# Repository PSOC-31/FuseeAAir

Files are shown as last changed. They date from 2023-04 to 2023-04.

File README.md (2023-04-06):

# FuseeAAir
Sources matérielles et pédagogiques autour des fusées à air utilisées à Planète Sciences Occitanie
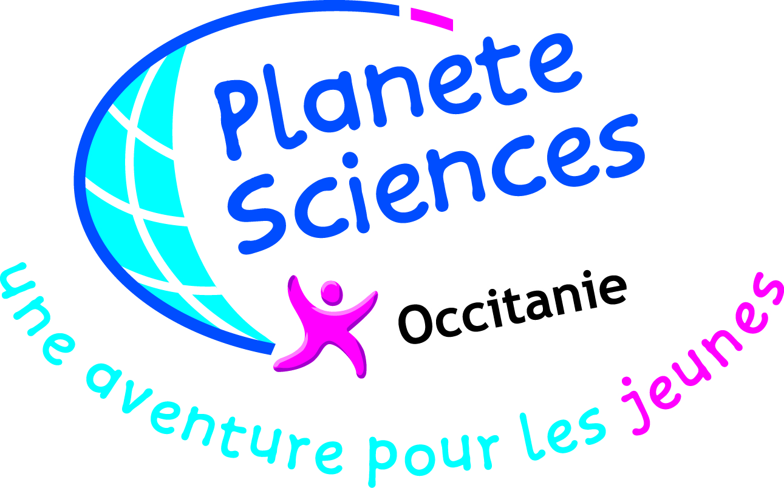
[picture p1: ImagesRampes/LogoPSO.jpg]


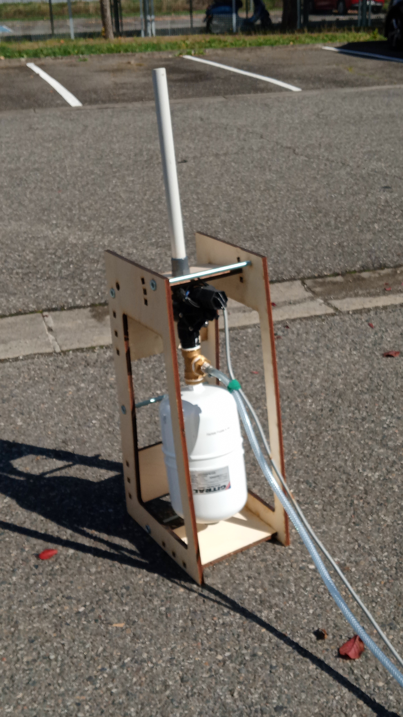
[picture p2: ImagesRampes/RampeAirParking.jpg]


## Notes de versions. 

Attention, les versions citées sont celles des versions matérielles, non pas celles du présent document, lui-même bien moins souvent mis à jour que le matériel.

-   V1 Base initiale dont le réservoir d'air est constitué d'un tube PVC pour conduite d'eau pression (genre piscine) diamètre 90 (à vérifier) , d'un raccord en T et divers raccords et bouchons. A été reproduit en quelques exemplaires, mais chaque fois avec des fuites sans possibilité de rattrapage parce que non-démontable.

-   V2 Version dont le réservoir est constitué d'un raccord femelle-femelle diamètre 100, d'un tampon de visite et de divers raccord. Présente l'avantage d'être démontable pour rattraper les mauvais collages, mais nous avons eu des explosions lors d'animations.

-   V3 Version dont le réservoir est constitué d'un vase d'expansion vendu garanti pour 10 bars.

    -   V 3.0 Version initiale. Le support bois découpé laser consomme 4 planches 300\*600 e10.
    -   V 3.1 Support bois à flancs ajourés sur 2 planches.
    -   V3.2 Divers ajustements sur le support. Quelques problèmes récurrents d'introduction en travers des raccords métal/plastique.
    -   V 3.3 Utilisation d'un T 1 pouce au lieu de 3/4 de pouce, ce qui permet de limiter les destructions de filetages plastique, en particulier au niveau de l'électro-vanne. Ajustement du support.
    -   V 3.4 Ajustement du support.
    -   V3.5 Version de travail du document de fabrication intermédiaire
    -   V3.6 Mise au propre des documents pour publication sur https://github.com/PSOC-31

## Inventaire des éléments

  ---------------------------------------------------------------------------- ----------------------------------------- --------------------- ----------------- ------ ------- -------
  Electro vanne                                                                1\" FF JTV 9V RBIRD                       IrriJardin            421020            1      49,99   54,42
  Vase d'expension Gitral HY5                                                  Partedis                                  Partedis              17119             1      54,42   54,42
  Tube renforcé 7\*13                                                          rlx 25m pvc tresse 7\*13                  CIR                   1025V130007       5      45,72   9,14
  Té laiton FFF 26X34 1pouce                                                                                             Partedis              29407             1      8,3     8,3
  Réduction laiton MF 6 pans JT plat 26-20                                                                               Partedis              68472             1      2,54    2,54
  Réduction laiton MF 6 pans JT plat 26-15                                                                               Partedis              68467             1      3,91    3,91
  Réduction laiton MF 6 pans JT plat 15-8                                                                                Partedis              68320             1      1,06    1,06
  Mamelon MM 6 pans plastique 1pouce                                                                                     IrriJardin            181755            1      5       5
  Tétine (à refaire)                                                           douille cann male co.gaz                  CIR                   1230717           1      5,55    5,55
  Collier                                                                      6 colliersgalva 9-16 sachet l8mm          Leroy Merlin Balma    h 80153727        2      3,25    1,08
  Pompe a pied 500                                                             Pompe a pied 500                          Decatlon escalquens   1829519           1      16      16
  Valve pour roue voiture                                                                                                Feu Vert                                1      0       0
  Raccord fileté PVC                                                           Raccord fil Pvc M32 F25 26\*34            IrriJardin            120639            1      3,4     3,4
  Tube IRO                                                                     Tube tulipe irl lm d25mm gris 2.5m        Leroy Merlin Balma    h3447640069375    0,35   1,35    0,19
  Tampon de visite d40                                                         bouchon D40                               Leroy Merlin Balma    h 3343340668804   2      0,65    1,3
  Manchon ff d40                                                               Manchon ff d40                            Leroy Merlin Balma    h 3343340465205   2      0,25    0,5
  Tube écoulement d40                                                                                                    Leroy Merlin Balma                      2      0,15    0,15
  Fil électrique double conducteur, double isolation, souple.                                                                                                    6              0
  Connecteur pile 9V                                                                                                                                             1              0
  Interrupteur à bascule marche-arrêt 12mm avec couvercle de protection 1021   AliExpress                                088 electric Store                      1      1,89    1,89
  Pile 9V                                                                                                                Opitec                                  1      20,99   2,1
  Planche CTP 10 mm 300\*600                                                   FabRiquet                                                                         2      10      20
  Découpe laser                                                                FabRiquet                                                                         0,33   40      13,2
  Tige filetée M10                                                                                                       Castorama                               0,25   1,9     0,48
  Ecrou façon rondelle M10                                                     Ecrou emb. Crantée din -çé » ZG M10 X25   Bricoman                                4      5       0,8
  Rondelle large 10                                                            Rondelles extralarge ZG D10X36X2 X25      Bricoman                                4      3,58    0,57
  Ecrou papillon                                                                                                                                                 4      1,09    1,09
                                                                                                                                                                                
  Total                                                                                                                                                                         207,1
  ---------------------------------------------------------------------------- ----------------------------------------- --------------------- ----------------- ------ ------- -------

## Montage de la chambre de pression.

La chambre de pression est le volume d'air immédiatement à l'arrière de l'électrovanne. C'est le vase d'expansion, les divers raccords et le tuyau de gonflage qui sont sous pression, dans l'attente du lancement.

La première étape consiste a assembler entre eux les éléments de la chambre de pression afin qu'il ne forme qu'un seul élément.

## Généralités sur l'étanchéité.

L'ensemble des parties sous pression devront supporter plusieurs bars. L'étanchéité du montage des raccords est donc primordial. D'une façon générale, l'utilisation de joints est largement recommandé, mais pour cela il est nécessaire qu'une surface d'appui existe, ce qui n'est pas le cas dans l'ensemble des objets choisi. Après avoir essayé diverses solutions, de la pâte spécialisée au fil imprégné, ma préférence personnelle reste au ruban PTFE (Téflon, antonomase). Je recommande sur un montage métal-métal de faire au moins une dizaine de tours, dans le sens du dévissage pour éviter le déroulement lors de l'introduction. Si lors des essais en pression dans un bac d'eau, on voit apparaître des fuites, on peu démonter le raccord et ajouter des tours supplémentaires. Sur un raccord plastique-métal ou plastique-plastique, il faut généralement moins de tours.

Attention au début du vissage, on part très vite en travers, surtout dans les montages métal-plastique, et on a tendance à flinguer la partie plastique. Je recommande, lors de la pose du ruban PTFE, d'épargner les premiers millimètres. Ça aide à une introduction correcte.

## Montage des raccords.

-   Monter sur la partie perpendiculaire du raccord en T femelle/femelle/femelle 1 pouce (26X34), la réduction mâle-femelle 26-15.
-   Sur cette même réduction, monter une tétine mâle XXX pour tuyau 7\*13.
-   Sur une branche du T, monter un mamelon double mâle-mâle 1 pouce (26X34) en plastique.
-   Sur ce mamelon, monter l'électrovanne, coté entrée (empennage de la flèche sur l'électrovanne).
-   De l'autre coté de ce mamelon, en face sur l'autre branche du T, visser une réduction femelle-femelle 26-20.
-   Dans ce dernier mamelon, visser le vase d'expansion 5 litres.

## Montage de la ligne de gonflage.

Voir le document commun pour les rampes fusée à eau et rampes fusée à air « Fabrication de la ligne de gonflage pour Bases de lancement Fusées à Air et Fusées à Eau. V1.1 »

## Montage de la commande de l'électrovanne.

Il y a plusieurs types d'électrovannes. Certaines sont nominalement alimentées en 24V. Je suppose que c'est pour se prémunir contre les possibles pertes en lignes dues à de très longs câblages dans un champ. Pour une utilisation à notre pression, avec de l'air et avec un câblage soigné, une tension nominale de 9V est suffisante. Cependant, je recommande l'utilisation de piles alcalines.



Le boîtier de commande est un assemblage de tubes d'écoulement d'eau de diamètre 40.

Poncez-collez deux manchons femelle/femelle sur une longueur de tube de 60 mm. Au extrémités des manchons, collez les tampons de visite en ayant préalablement dévissé les bouchons des tampons.

Percez et usinez les bouchons pour, d'un coté, placer l'interrupteur,

 de l'autre pour faire passer un câble électrique type double conducteur, double isolation, souple, de 6 mètres.

Taillez un bout de polystyrène extrudé ou de la mousse un peu dure, diamètre 30, épaisseur 20, pour caler la pile 9V.



Montez et câblez un interrupteur sur un bouchon de tampon. Vissez ce bouchon et câblez le connecteur de pile et le câble secteur. Bien sûr, vous n'avez pas oublié de faire passer ce câble dans le trou de l'autre bouchon!

Glissez d'abord la cale en polystyrène, puis la pile connectée. Placez un collier de serrage plastique (Rislan ou Colson, antonomase ) sur le câble, et serrez bien. Vissez le bouchon en faisant quelques tours en arrière avant de visser (pour éviter d'avoir un câble vrillé à l'intérieur).

Connectez l'électrovanne à l'autre extrémité en soudant et utilisant de la gaine gaine thermo-rétractable et thermo-collante.

Fixez le câble à l'électro-vanne avec un collier de serrage plastique (Rislan ou Colson, antonomase ).

## Configuration du vase d'expansion.

Le vase d'expansion est prévu pour permettre une dilatation de l'eau dans un circuit (cas de la partie chaude de l'eau sanitaire), sans mettre en contact l'eau avec l'air pour limiter l'oxydation des parties métalliques. Par construction, il existe une chambre à air intégrée dans le vase, gonflé à 2 bars. Pour notre utilisation, il est nécessaire de dégonfler entièrement cette chambre pour profiter de la vitesse maximum d'éjection de l'air. Donc, dans un premier temps, on va dévisser le protége-cul du vase, et appuyer avec un objet quelconque sur la valve pour dégonfler.

Photo à venir.

Ensuite, pressuriser avec la pompe à vélo le circuit principal (dans le vase, pour chasser le reste d'air de la chambre) et recommencer à appuyer sur la valve. Refaire 2 ou 3 fois cette opération pour vider complètement la chambre.

## Tests de l'ensemble.

Testez le montage en plongeant l'ensemble sous pression (2 bars mini) dans l'eau. N'oubliez pas de tester les deux extrémités du tuyau d'air.

Pour les raccords filetés, voir note «Généralités sur l'étanchéité» en début de notice.

Pour les raccords avec collier inox, un resserrage suffit la plupart du temps.

De plus, un test à pression élevé est recommandé (je dirais env 6 bars mais pas plus de 10, limite de la garantie du vase d'expansion) en prenant des précautions en cas d'éclatement, genre carton ou couverture autour. Attention, à forte pression, il arrive que l'électro-vanne ne se déclenche pas. La dépressurisation peux se faire à distance en déconnectant la pompe à vélo et agir mécaniquement sur la valve du tube. Pour une utilisation dans ces pressions, on peu envisager un déclenchement avec 2 plies 9v, donc 18v.

## Fabrication du support.

### Tube de lancement.

Coupez une longueur de 350 mm de tube IRO (isolant rigide ordinaire) ou IRL (isolant rigide lisse), et non pas ICTA (isolant cintrable transversalement annelé*), *vendu en rayon électricité, de diamètre 32. Collez-le sur un raccord fileté Pvc M32 F25 26\*34. Laisser sécher au moins 24h.

Cet ensemble tube/raccord sert au montage de l'ensemble actif de la rampe sur le support en bois et permet de rentrer une rampe, voire deux, dans une malle.

N'oubliez pas dans les achats les longueurs de tube IRO nécessaires en tant que mandrin pour la fabrication des fusées elles-mêmes. Leur nombre dépendra du nombre d'enfants par atelier.

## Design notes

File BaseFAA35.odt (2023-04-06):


Fabrication Bases de lancement Fusées à Air. V3.5

Photo à insérer

# Notes de versions.

Attention, les versions citées sont celles des versions matérielles, non pas celles du présent document, lui-même bien moins souvent mis à jour que le matériel.

- V1 Base initiale dont le réservoir d’air est constitué d’un tube PVC pour conduite d’eau pression (genre piscine) diamètre 90 (à vérifier) , d’un raccord en T et divers raccords et bouchons. A été reproduit en quelques exemplaires, mais chaque fois avec des fuites sans possibilité de rattrapage parce que non-démontable.
- V2 Version dont le réservoir est constitué d’un raccord femelle-femelle diamètre 100, d’un tampon de visite et de divers raccord. Présente l’avantage d’être démontable pour rattraper les mauvais collage, mais nous avons eu des explosions lors d’animations.
- V3 Version dont le réservoir est constitué d’un vase d’expansion vendu garanti pour 10 bars.
  - V 3.0 Version initiale. Le support bois découpé laser consomme 4 planches 300*600 e10.
  - V 3.1 Support bois à flancs ajourés sur 2 planches.
  - V3.2 Divers ajustements sur le support. Quelques problèmes récurrents d’introduction en travers des raccords métal/plastique.
  - V 3.3 Utilisation d’un T 1 pouce au lieu de 3/4 de pouce, ce qui permet de limiter les destructions de filetages plastique, en particulier au niveau de l’électro-vanne. Ajustement du support.
  - V 3.4 Ajustement du support.

# Inventaire des éléments

Tableau à venir

# Montage de la chambre de pression.

La chambre de pression est le volume d’air immédiatement à l’arrière de l’électrovanne. C’est le vase d’expansion, les divers raccords et le tuyau de gonflage qui sont sous pression, dans l’attente du lancement.

La première étape consiste a assembler entre eux les éléments de la chambre de pression afin qu’il ne forme qu’un seul élément.

## Généralités sur l’étanchéité.

L’ensemble des parties sous pression devront supporter plusieurs bars. L’étanchéité du montage des raccords est donc primordial. D’une façon générale, l’utilisation de joints est largement recommandé, mais pour cela il est nécessaire qu’une surface d’appui existe, ce qui n’est pas le cas dans l’ensemble des objets choisi. Après avoir essayé diverses solutions, de la pâte spécialisée au fil imprégné, ma préférence personnelle reste au ruban PTFE (Téflon, antonomase). Je recommande sur un montage métal-métal de faire au moins une dizaine de tours, dans le sens du dévissage pour éviter le déroulement lors de l’introduction. Si lors des essais en pression dans un bac d’eau, on voit apparaître des fuites, on peu démonter le raccord et ajouter des tours supplémentaires. Sur un raccord plastique-métal ou plastique-plastique, il faut généralement moins de tours.

Attention au début du vissage, on part très vite en travers, surtout dans les montages métal-plastique, et on a tendance à flinguer la partie plastique. Je recommande, lors de la pose du ruban PTFE, d’épargner les premiers millimètres. Ça aide à une introduction correcte.

# Montage de la ligne de gonflage.

Voir le document commun pour les rampes fusée à eau et rampes fusée à air « Fabrication de la ligne de gonflage pour Bases de lancement Fusées à Air et Fusées à Eau. V1.1 »

# Montage de la commande de l’électrovanne.

Nominalement, l’électrovanne est alimenté en 24V. Je suppose que c’est pour se prémunir contre les possibles pertes en lignes dues à de très longs câblages dans un champ. Pour une utilisation à notre pression, avec de l’air et avec un câblage soigné, une tension nominale de 9V est suffisante. Cependant, je recommande l’utilisation de piles alcalines.

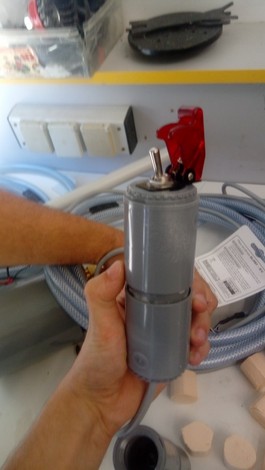
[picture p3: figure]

Le boîtier de commande est un assemblage de tubes d’écoulement d’eau de diamètre 40.

Poncez-collez deux manchons femelle/femelle sur une longueur de tube de 60 mm. Au extrémités des manchons, collez les tampons de visite en ayant préalablement dévissé les bouchons des tampons.

Percez et usinez les bouchons pour, d’un coté, placer l’interrupteur, de l’autre pour faire passer un câble électrique type double conducteur, double isolation, souple, de 6 mètres.

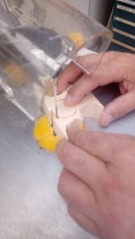
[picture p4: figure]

Taillez un bout de polystyrène extrudé diamètre 30, épaisseur 20, pour caler la pile 9V.

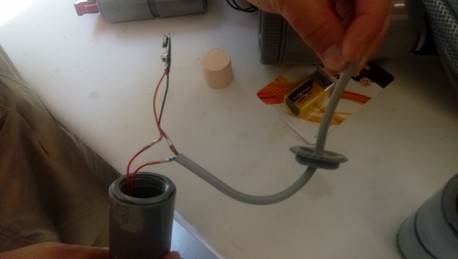
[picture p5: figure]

Montez et câblez un interrupteur sur un bouchon de tampon. Vissez ce bouchon et câblez le connecteur de pile et le câble secteur. Bien sûr, vous n’avez pas oublié de faire passer ce câble dans le trou de l’autre bouchon!

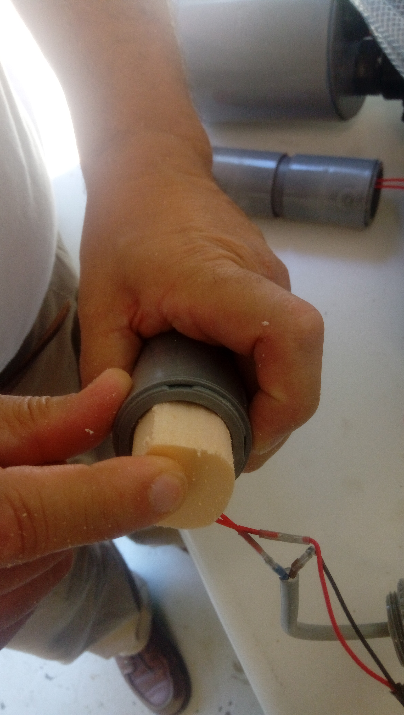
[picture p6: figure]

Glissez d’abord la cale en polystyrène, puis la pile connectée. Placez un collier de serrage plastique (Rislan ou Colson, antonomase ) sur le câble, et serrez bien. Vissez le bouchon en faisant quelques tours en arrière avant de visser (pour éviter d’avoir un câble vrillé à l’intérieur).

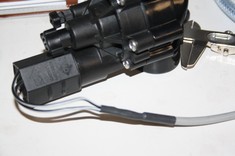
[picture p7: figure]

Connectez l’électrovanne à l’autre extrémité en soudant et utilisant de la gaine gaine thermo-rétractable et thermo-collante.

Fixez le câble à l’électro-vanne avec un collier de serrage plastique (Rislan ou Colson, antonomase ).

Photo à venir.

# Tests de l’ensemble.

Testez le montage en plongeant l’ensemble sous pression (2 bars mini) dans l’eau. N’oubliez pas de tester les deux extrémités du tuyau d’air.

Pour les raccords filetés, voir note «Généralités sur l’étanchéité» en début de notice.

Pour les raccords avec collier inox, un resserrage suffit la plupart du temps.

De plus, un test à pression élevé est recommandé (je dirais env 6 bars mais pas plus de 10, limite de la garantie du vase d’expansion) en prenant des précautions en cas d’éclatement, genre carton ou couverture autour. Attention, à forte pression, il arrive que l’électro-vanne ne se déclenche pas. La dépressurisation peux se faire à distance en déconnectant la pompe à vélo et agir mécaniquement sur la valve du tube. Pour une utilisation dans ces pressions, on peu envisager un déclenchement avec 2 plies 9v, donc 18v.

# Fabrication du support.

# Tube de lancement.

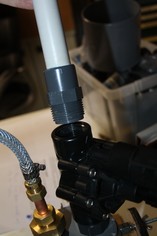
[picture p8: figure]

Coupez une longueur de 350 mm de tube IRO (isolant rigide ordinaire) ou IRL (isolant rigide lisse), et non pas ICTA (isolant cintrable transversalement annelé), vendu en rayon électricité, de diamètre 32. Collez-le sur un raccord fileté Pvc M32 F25 26*34. Laisser sécher au moins 24h.

Cet ensemble tube/raccord sert au montage de l’ensemble actif de la rampe sur le support en bois et permet de renter une rampe, voire deux, dans une malle.

N’oubliez pas dans les achats les longueurs de tube IRO nécessaires en tant que mandrin pour la fabrication des fusées elles-mêmes. Leur nombre dépendra du nombre d’enfants par atelier.

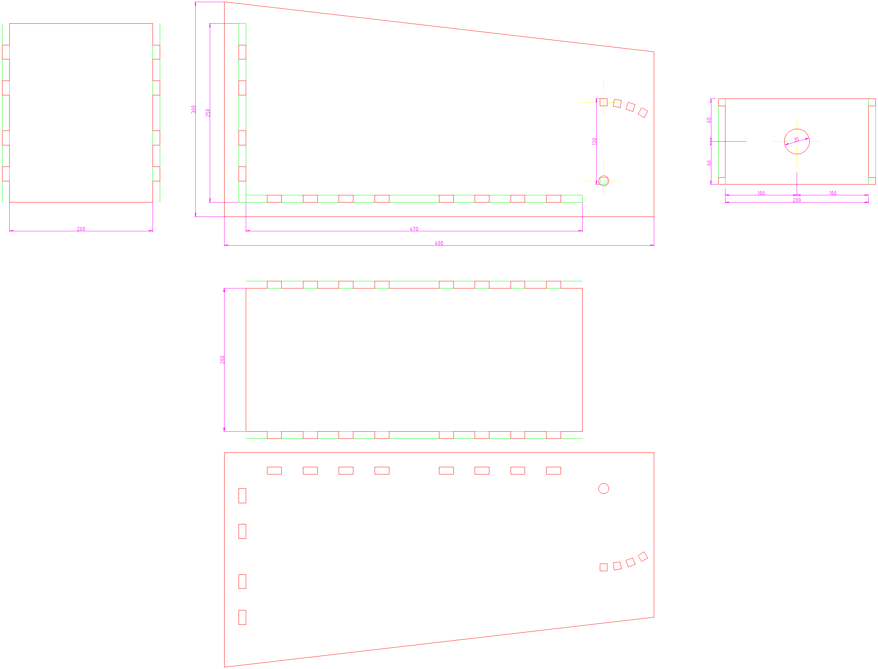
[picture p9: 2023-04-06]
SupportFAAv3.png

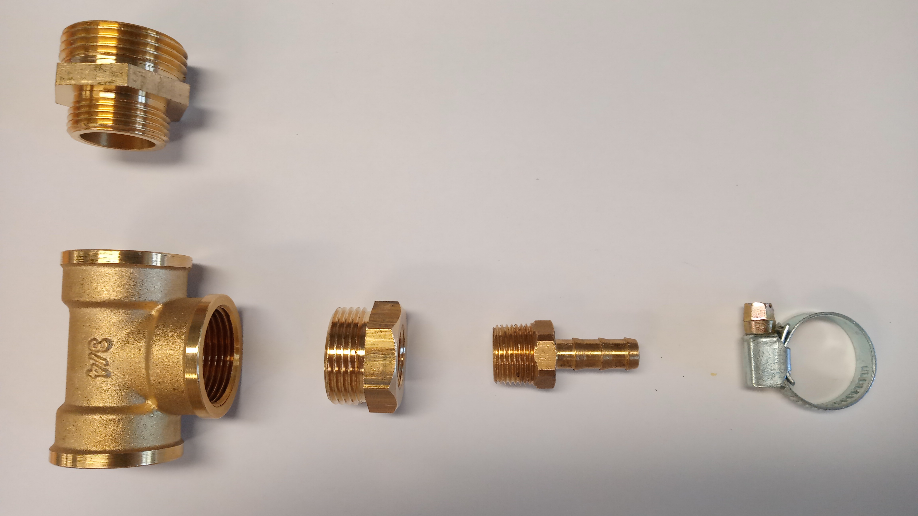
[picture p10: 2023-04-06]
ImagesRampes/Raccords.jpg

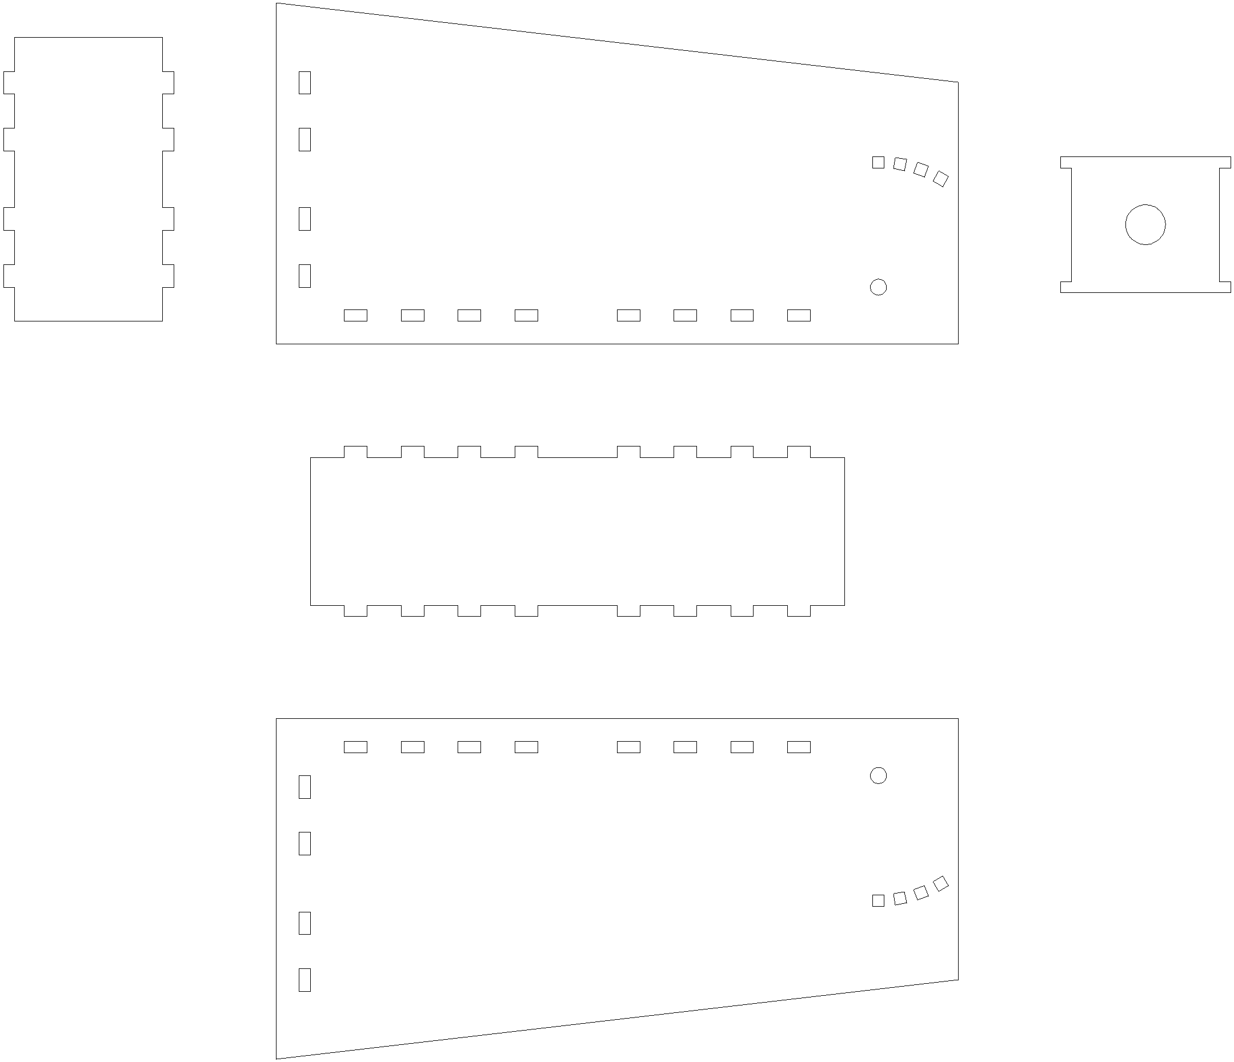
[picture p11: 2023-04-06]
20/SupportFAAv2.png

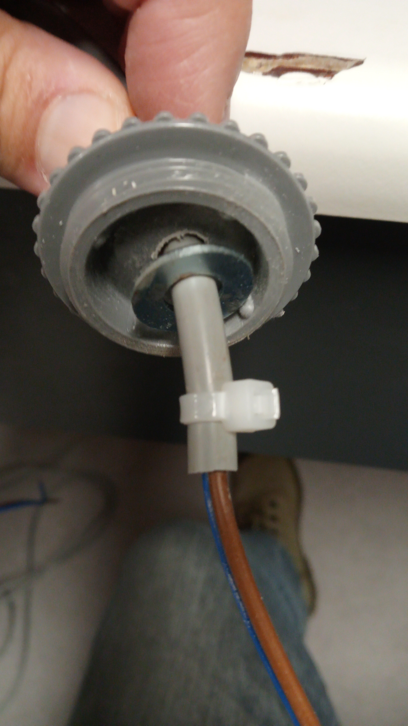
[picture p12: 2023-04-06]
ImagesRampes/CommandeDetailCable.jpg

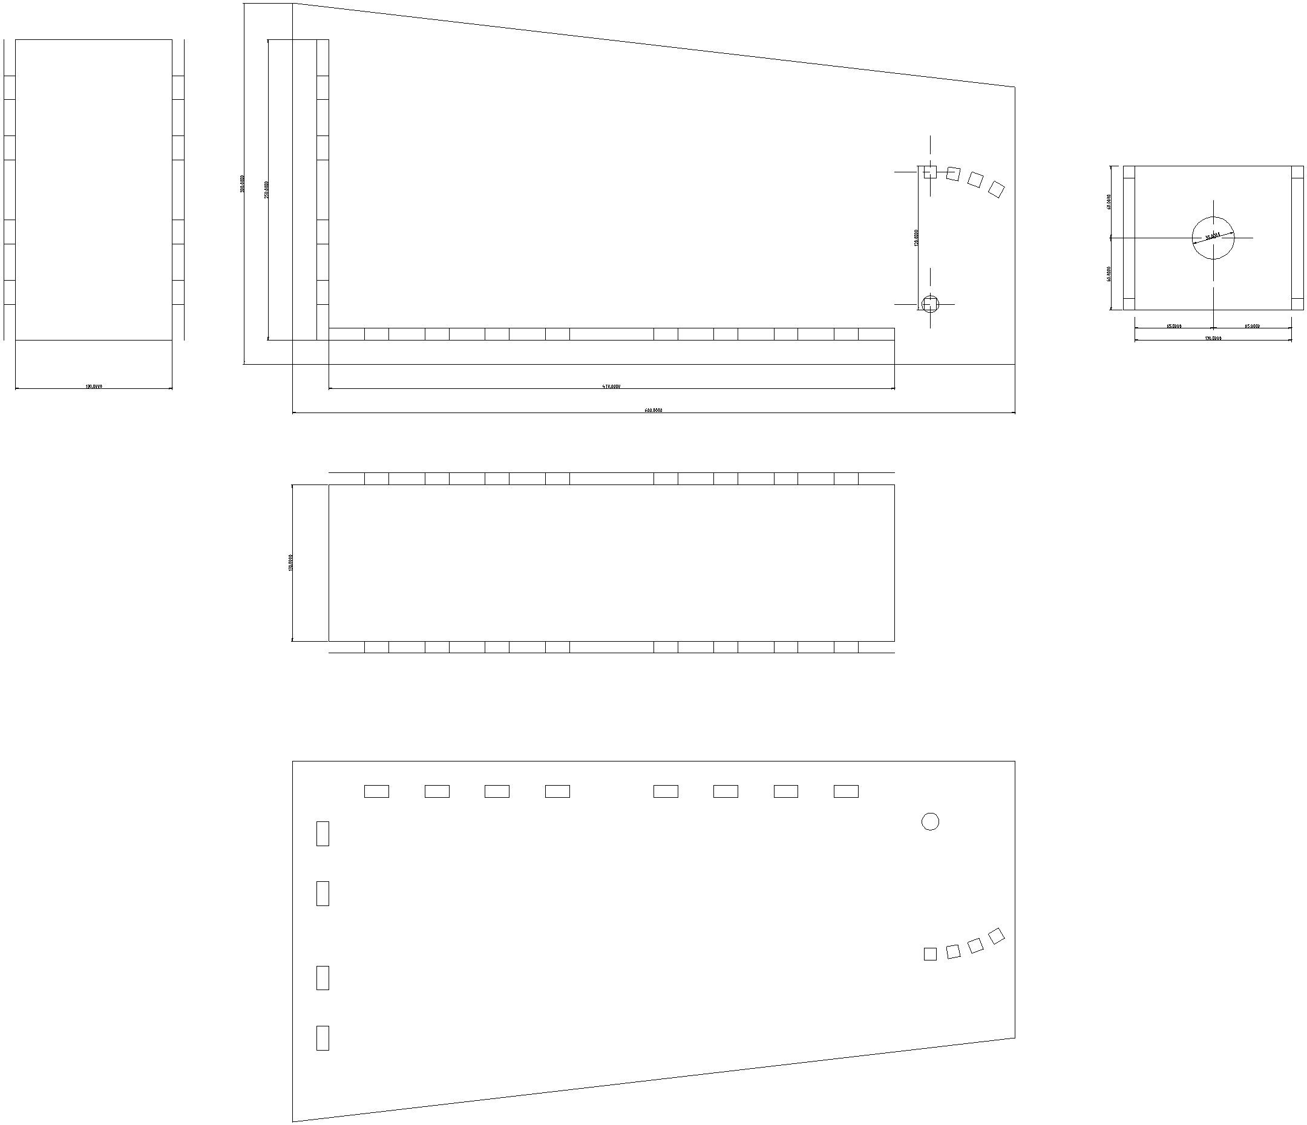
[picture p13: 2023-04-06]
20/SupportFAAv2Integral.png

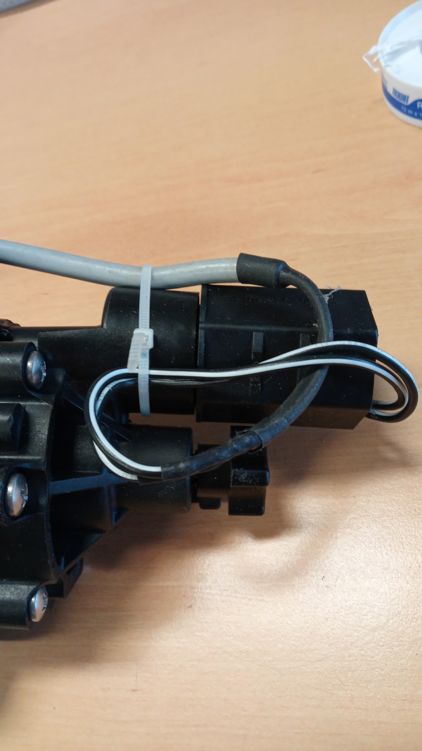
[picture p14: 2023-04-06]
ImagesRampes/ElectrovanneCablageFixation.jpg

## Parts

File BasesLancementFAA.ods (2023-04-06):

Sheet: Fournisseurs
Vase d’expension Gitral HY5 | PROLIANS BERNARD PAGES - Toulouse Montaudran | Z.I. de, 4 Rue Claude Gonin, 31400 Toulouse | 05 61 36 83 00 | non
Vase d’expension Gitral HY5 | LRI - SODIME (La robinetterie industrielle) | 26 Av. Didier Daurat, 31400 Toulouse | 05 34 25 64 00 | non
Vase d’expension Gitral HY5 | Sisca | Imp. Didier Daurat, 31400 Toulouse | 05 61 34 09 17 | n’existe plus
Vase d’expension Gitral HY5 | CEDEO Toulouse Sud : Sanitaire - Chauffage - Plomberie | 290 Rue Léon Joulin, 31100 Toulouse | 07 55 54 66 83 | 2 en stock
Vase d’expension Gitral HY5 | Brossette | 290 Rue Léon Joulin, 31100 Toulouse | 05 61 19 02 50
Vase d’expension Gitral HY5 | Frans Bonhomme Toulouse Sud | ZI Thibaud, 20 Rue Boudeville, 31100 Toulouse | 05 61 44 22 23
Vase d’expension Gitral HY5
Vase d’expension Gitral HY5
Vase d’expension Gitral HY5
Vase d’expension Gitral HY5

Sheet: FAAv3.4
Base de lancement fusées à air | Nom fournisseur | Unité de vente | Fournisseur | Rf Fournisseur | Nb par rampe | Prix unitaire | Norme de prix | Prix TTC | Prix par rampe | Lien Internet | Taxe
Electro-vanne | Vanne Electrique 1" 100DVF | 1 | Frans Bonhomme | 67287N | 1 | 35,02 | HT | 42,02 | 42,02 |  | 20
Vase d’expension Gitral HY5 | Partedis |  | Partedis |  | 1 | 0,00 | HT | 0,00 | #DIV/0 !
Tube renforcé 7*13 | rlx 25m pvc tresse 7*13 | 25 | CIR | 1025V130007 | 5 | 38,10 | HT | 45,72 | 9,14
Tétine (à refaire) | douille cann male co.gaz | 1 | CIR | 1230717 | 1 | 5,55 | TTC | 5,55 | 5,55
collier | collier bande TUY 13 L8 Boutte ou ↓ | 2 | Leroy Merlin Balma | h 60463410 | 2 | 5,10 | HT | 6,12 | 6,12
Collier | Collier inox 9-16 l8 ou ↓ | 2 | Leroy Merlin Balma | h 80153716 | 2 | 3,25 | HT | 3,90 | 3,90
Collier | 6 colliersgalva 9-16 sachet l8mm | 6 | Leroy Merlin Balma | h 80153727 | 2 | 3,25 | TTC | 3,25 | 1,08
Pompe a pied 500 | Pompe a pied 500 | 1 | Decatlon escalquens | 1829519 | 1 | 16,00 | TTC | 16,00 | 16,00
Valve pour roue voiture |  | 1 | Feu Vert |  | 1 | 0,00 | TTC | 0,00 | 0,00
Raccord fileté PVC | Raccord fil Pvc M32 F25 26*34 | 1 | IrriJardin | 120639 | 1 | 3,40 | TTC | 3,40 | 3,40
Tube IRO | Tube tulipe irl lm d25mm gris 2.5m | 2,5 | Leroy Merlin Balma | h3447640069375 | 0,35 | 1,35 | TTC | 1,35 | 0,19
Tampon de visite d40 | bouchon D40 | 1 | Leroy Merlin Balma | h 3343340668804 | 2 | 0,65 | TTC | 0,65 | 1,30
Manchon ff d40 | Manchon ff d40 | 1 | Leroy Merlin Balma | h 3343340465205 | 2 | 0,25 | TTC | 0,25 | 0,50
Tube écoulement d40 |  | 2 | Leroy Merlin Balma |  | 2 | 0,15 | TTC | 0,15 | 0,15
Fil électrique double conducteur, double isolation, souple. |  | 1 |  |  | 6 |  |  | 0,00 | 0,00
Connecteur pile 9V |  | 1 |  |  | 1 |  |  | 0,00 | 0,00
Interrupteur à bascule marche-arrêt 12mm avec couvercle de protection 1021 | AliExpress | 1 | 088 electric Store |  | 1 | 1,89 |  | 1,89 | 1,89 | https://fr.aliexpress.com/item/32904395565.html
Pile 9V |  | 1 |  |  | 1 |  |  | 0,00 | 0,00
Planche CTP 10 mm 300*600 | FabRiquet | 1 |  |  | 2 |  |  | 0,00 | 0,00
Découpe laser | FabRiquet | 1 |  |  |  |  |  | 0,00 | 0,00
 |  | 1
Total |  |  |  |  |  |  |  |  | #DIV/0 !

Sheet: FAAv3.0
Base de lancement fusées à air | Nom fournisseur | Unité de vente | Fournisseur | Rf Fournisseur | Nb par rampe | Prix unitaire | Norme de prix | Prix TTC | Prix par rampe | Lien Internet | Taxe
Electro-vanne | Vanne Electrique 1" 100DVF | 1 | Frans Bonhomme | 67287N | 1 | 35,02 | HT | 42,02 | 42,02 |  | 20
Tube renforcé 7*13 | rlx 25m pvc tresse 7*13 | 25 | CIR | 1025V130007 | 5 | 38,10 | HT | 45,72 | 9,14
Tétine (à refaire) | douille cann male co.gaz | 1 | CIR | 1230717 | 1 | 5,55 | TTC | 5,55 | 5,55
Collier | Collier inox 9-16 l8 ou ↓ | 2 | Leroy Merlin Balma | h 80153716 | 2 | 3,25 | HT | 3,90 | 3,90
Collier | 6 colliersgalva 9-16 sachet l8mm | 6 | Leroy Merlin Balma | h 80153727 | 2 | 3,25 | TTC | 3,25 | 1,08
Pompe a pied 500 | Pompe a pied 500 | 1 | Decatlon escalquens | 1829519 | 1 | 16,00 | TTC | 16,00 | 16,00
Valve pour roue voiture |  |  | Feu Vert |  | 1 | Un pack de bière |  | Un pack de bière | #VALEUR !
Raccord fileté PVC | Raccord fil Pvc M32 F25 26*34 | 1 | IrriJardin | 120639 | 1 | 3,40 | TTC | 3,40 | 3,40
Tube IRO | Tube tulipe irl lm d25mm gris 2.5m | 2,5 | Leroy Merlin Balma | h3447640069375 | 0,35 | 1,35 | TTC | 1,35 | 0,19
Tampon de visite d40 | bouchon D40 | 1 | Leroy Merlin Balma | h 3343340668804 | 2 | 0,65 | TTC | 0,65 | 1,30
Manchon ff d40 | Manchon ff d40 | 1 | Leroy Merlin | h 3343340465205 | 2 | 0,25 | TTC | 0,25 | 0,50
Tube écoulement d40 |  | 2 |  |  | 2 | 0,15 | TTC | 0,15 | 0,15
Fil électrique double conducteur, double isolation, souple. |  |  |  |  | 6 |  |  | 0,00 | #DIV/0 !
Connecteur pile 9V |  |  |  |  | 1 |  |  | 0,00 | #DIV/0 !
Interrupteur à bascule marche-arrêt 12mm avec couvercle de protection 1021 | AliExpress |  | 088 electric Store |  | 1 | 1,89 |  | 1,89 | #DIV/0 ! | https://fr.aliexpress.com/item/32904395565.html
Pile 9V |  |  |  |  | 1 |  |  | 0,00 | #DIV/0 !
 |  |  |  |  |  |  |  | 0,00 | #DIV/0 !
 |  |  |  |  |  |  |  | 0,00 | #DIV/0 !

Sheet: FAAv2,0
Base de lancement fusées à air | Nom fournisseur | Unité de vente | Fournisseur | Rf Fournisseur | Nb par rampe | Prix unitaire | Norme de prix | Prix TTC | Prix par rampe | Lien Internet | Taxe
Electro-vanne | Vanne Electrique 1" 100DVF | 1 | Frans Bonhomme | 67287N | 1 | 35,02 | HT | 42,02 | 42,02 |  | 20
Tube renforcé 7*13 | rlx 25m pvc tresse 7*13 | 25 | CIR | 1025V130007 | 5 | 38,10 | HT | 45,72 | 9,14
Tétine (à refaire) | douille cann male co.gaz | 1 | CIR | 1230717 | 1 | 5,55 | TTC | 5,55 | 5,55
collier | collier bande TUY 13 L8 Boutte ou ↓ | 2 | Leroy Merlin Balma | h 60463410 | 2 | 5,10 | HT | 6,12 | 6,12
Collier | Collier inox 9-16 l8 ou ↓ | 2 | Leroy Merlin Balma | h 80153716 | 2 | 3,25 | HT | 3,90 | 3,90
Collier | 6 colliersgalva 9-16 sachet l8mm | 6 | Leroy Merlin Balma | h 80153727 | 2 | 3,25 | TTC | 3,25 | 1,08
Tampon de visite d100 | Tampon de visite Nicoll | 1 | SIDV | 4rpevft | 1 | 5,34 | TTC | 5,34 | 5,34
Pompe a pied 500 | Pompe a pied 500 | 1 | Decatlon escalquens | 1829519 | 1 | 16,00 | TTC | 16,00 | 16,00
Manchon ff 100 |  | 1 |  |  | 1 |  | TTC | 0,00 | 0,00
tampon réducteur 100*32*32 |  | 1 | Cedeo | 1734105 | 1 | 6,34 | TTC | 6,34 | 6,34
embout fil mf red |  |  |  |  |  |  | TTC | 0,00 | #DIV/0 !
joint en caoutchouc 26*34 | 5 joint caoutchouc 26*34(2) | 5 | Leroy Merlin | h 68269152 | 1 | 2,00 | TTC | 2,00 | 0,40
joint en caoutchouc 20*27 | 10 joint caoutchouc 20*27 | 10 |  |  |  |  |  | 0,00 | 0,00
Valve pour roue voiture |  |  | Feu Vert |  |  | Un pack de bière |  | Un pack de bière | #VALEUR !
Raccord fileté PVC | Raccord fil Pvc M32 F25 26*34 | 1 | IrriJardin | 120639 | 3 | 3,40 | TTC | 3,40 | 10,20
Raccord 2 écrous prisonnier | Raccord 2 écrous prisonnier F15*21 12*17 | 1 | Leroy Merlin Balma | h 33699390927234 | 1 | 3,95 | TTC | 3,95 | 3,95
Tube IRO | Tube tulipe irl lm d25mm gris 2.5m | 2,5 | Leroy Merlin Balma | h3447640069375 | 0,35 | 1,35 | TTC | 1,35 | 0,19
Tampon de visite d40 | bouchon D40 | 1 | Leroy Merlin Balma | h 3343340668804 | 2 | 0,65 | TTC | 0,65 | 1,30
Manchon ff d40 | Manchon ff d40 | 1 | Leroy Merlin | h 3343340465205 | 2 | 0,25 | TTC | 0,25 | 0,50
Collier gouttière | collier embase taraudée acier galva d100 | 1 | Leroy Merlin Balma | 376017520111 | 2 | 1,85 | TTC | 1,85 | 3,70
Vis de fixation pour collier gouttière |  |  |  |  | 2 |  |  | 0,00 | #DIV/0 !
Écrou façon rondelle M6 |  |  |  |  | 2 |  |  | 0,00 | #DIV/0 !
Rondelle éventail M6 |  |  |  |  | 2 |  |  | 0,00 | #DIV/0 !
Écrou papillon M6 |  |  |  |  | 2 |  |  | 0,00 | #DIV/0 !
Tube écoulement d40 |  | 2 |  |  | 2 | 0,15 | TTC | 0,15 | 0,15
Fil électrique double conducteur, double isolation, souple. |  |  |  |  | 6 |  |  | 0,00 | #DIV/0 !
Connecteur pile 9V |  |  |  |  | 1 |  |  | 0,00 | #DIV/0 !
Interrupteur à bascule marche-arrêt 12mm avec couvercle de protection 1021 | AliExpress |  | 088 electric Store |  | 1 | 1,89 |  | 1,89 | #DIV/0 ! | https://fr.aliexpress.com/item/32904395565.html
 |  |  |  |  |  |  |  | 0,00 | #DIV/0 !
 |  |  |  |  |  |  |  | 0,00 | #DIV/0 !
 |  |  |  |  |  |  |  | 0,00 | #DIV/0 !

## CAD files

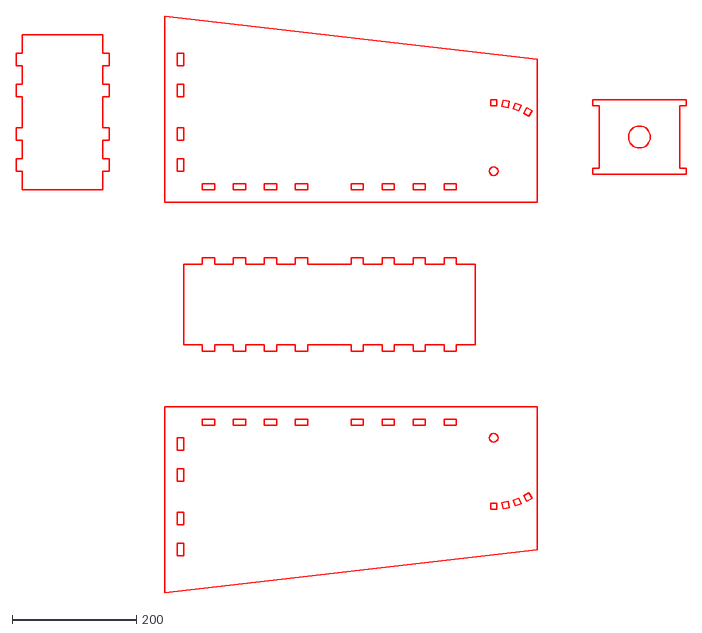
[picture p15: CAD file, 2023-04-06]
20/SupportFAAv2.0.dxf
1080.0 x 930.0

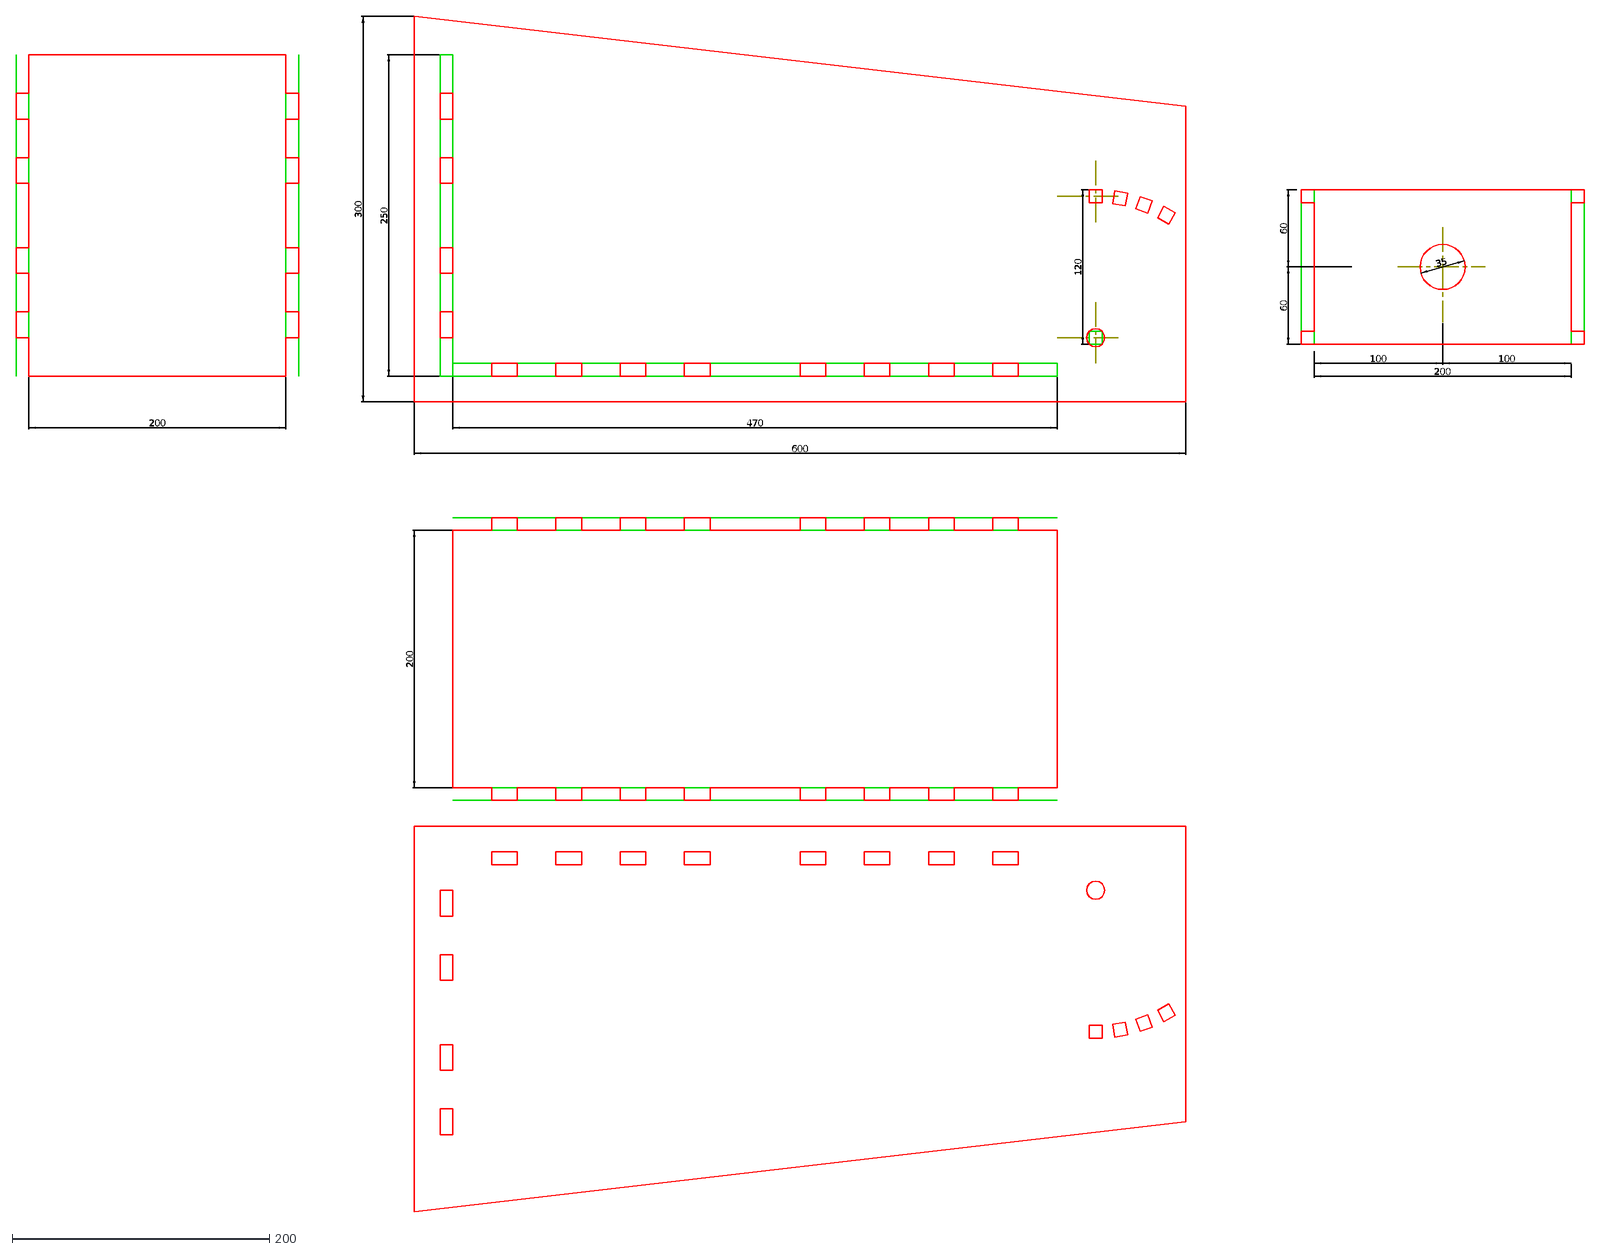
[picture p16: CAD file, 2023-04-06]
31/SupportFAA31Global.dxf
120
470
250
300
600
60
200
35
100

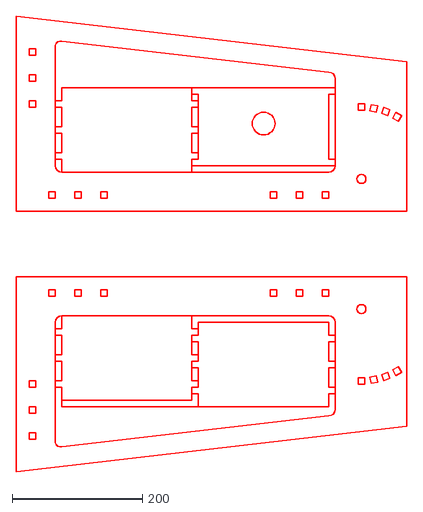
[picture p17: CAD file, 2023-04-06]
32/SupportFAA32Global.dxf
600.0 x 700.0

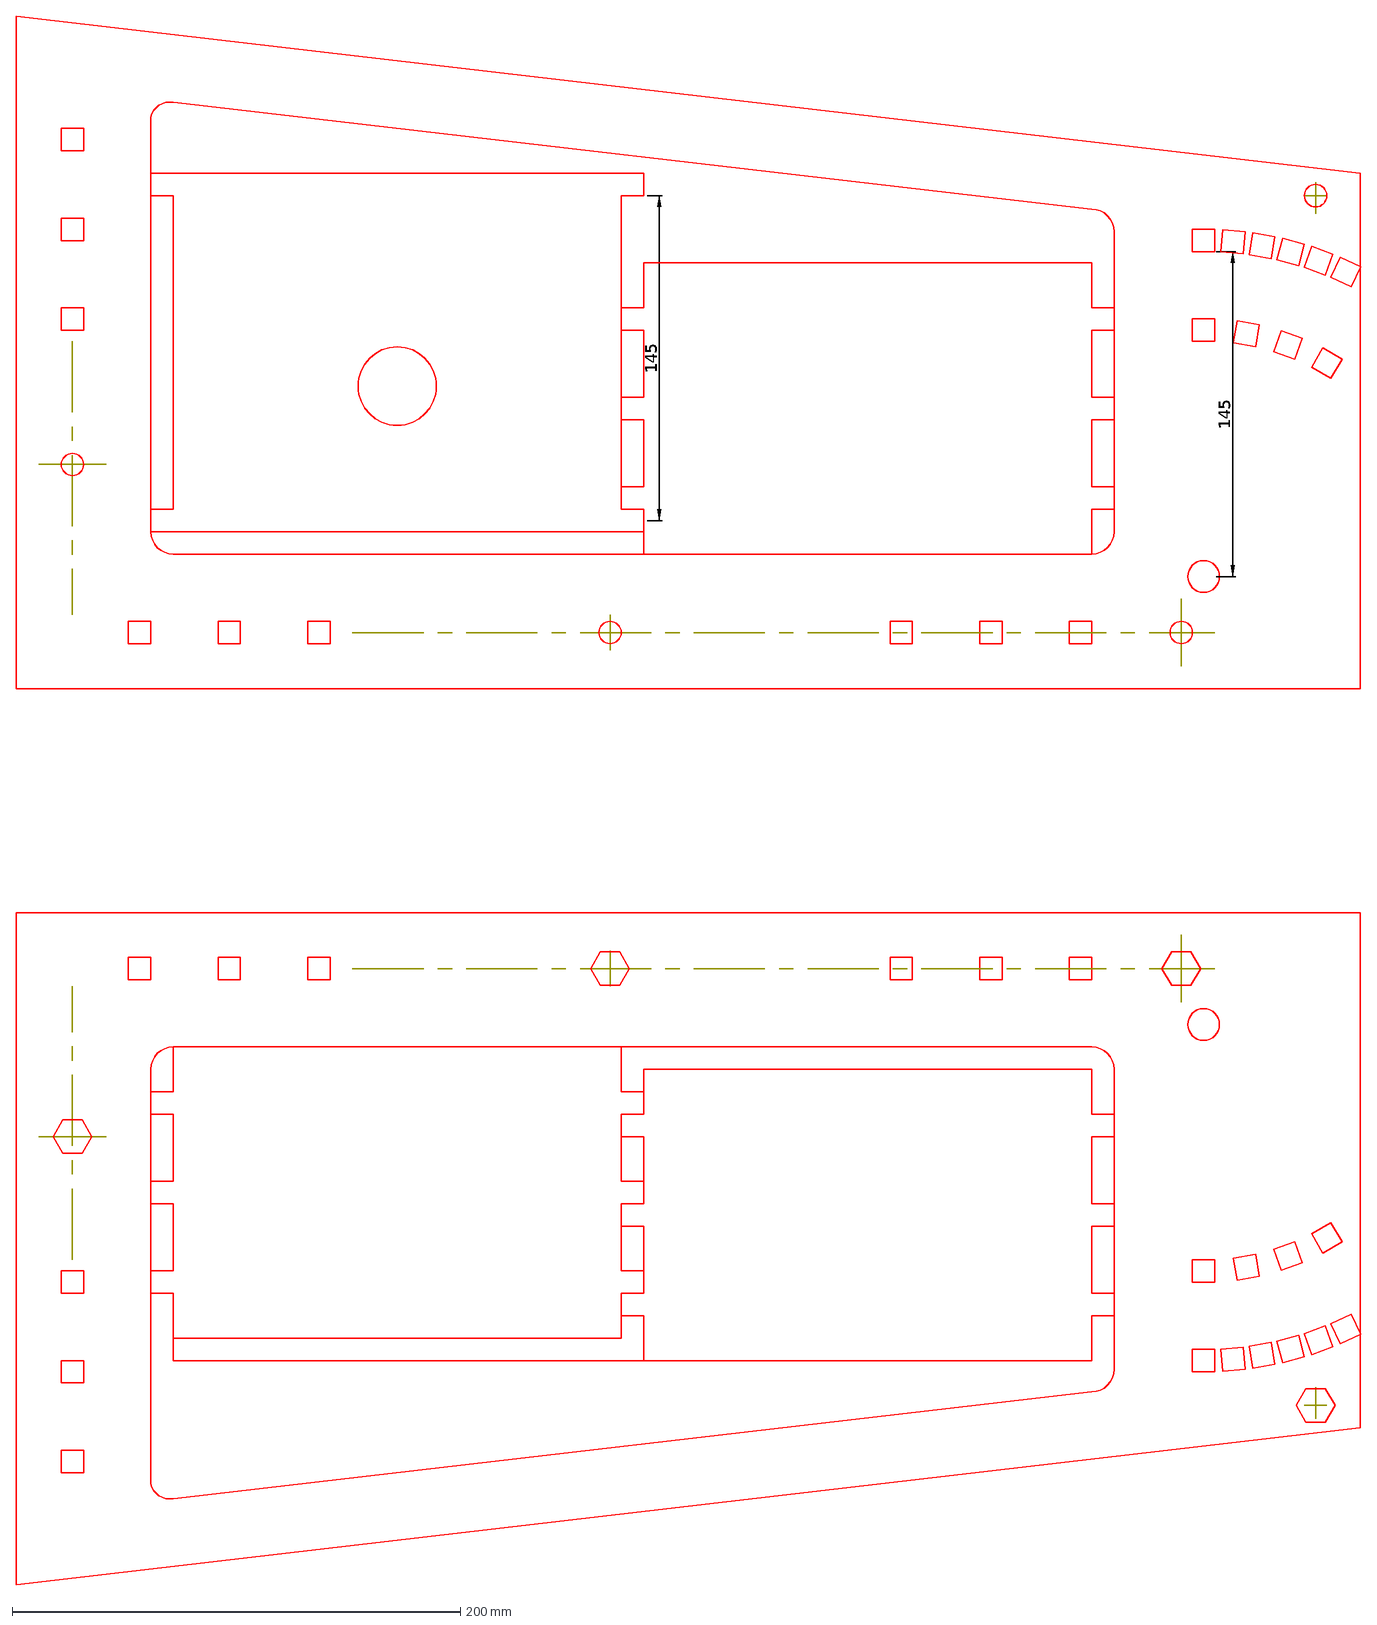
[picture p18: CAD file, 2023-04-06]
33/SupportFAA33Global.dxf
145

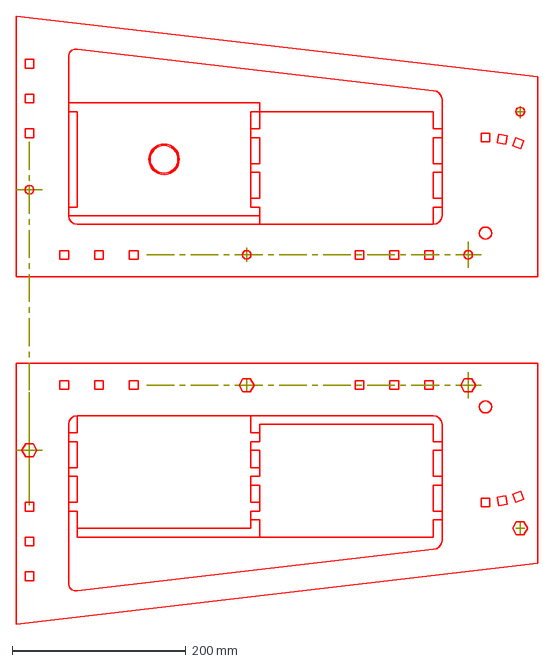
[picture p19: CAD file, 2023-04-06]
34/SupportFAA34Global.dxf
600.0 x 700.0 mm

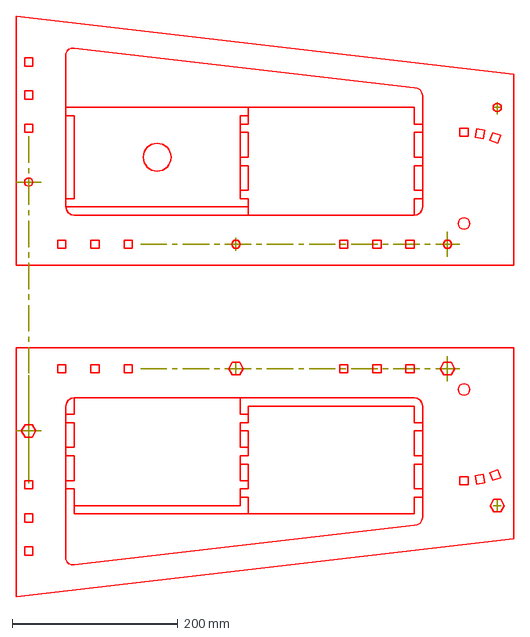
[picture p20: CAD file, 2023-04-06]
35/SupportFAA35Global.dxf
600.0 x 700.0 mm

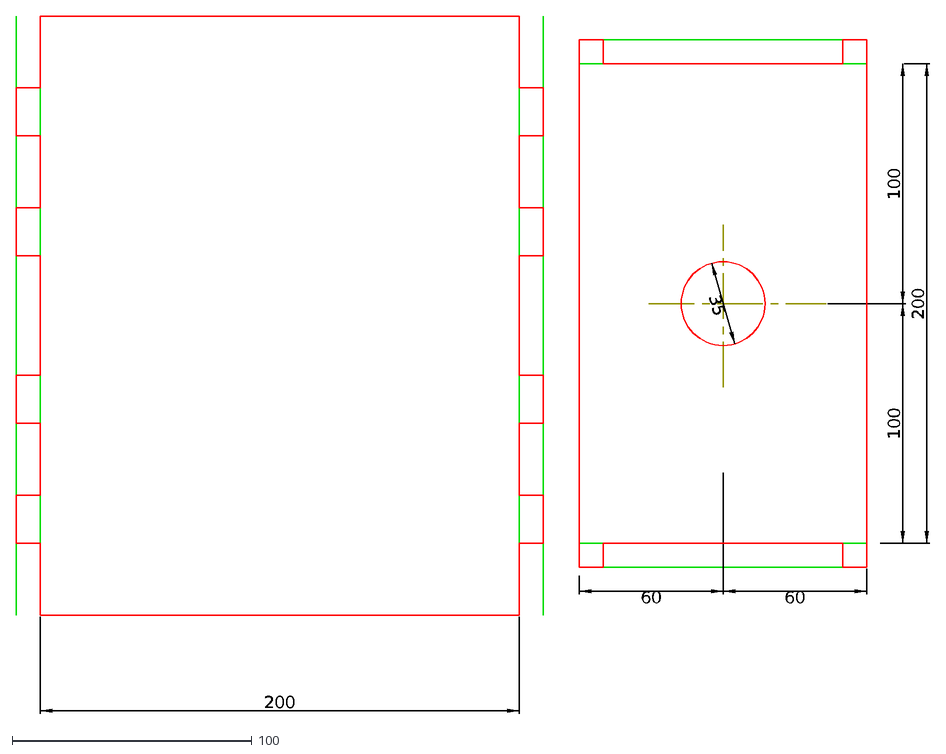
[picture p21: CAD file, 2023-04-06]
31/SupportFAA31TraversesHorizontales.dxf
200
60
35
100

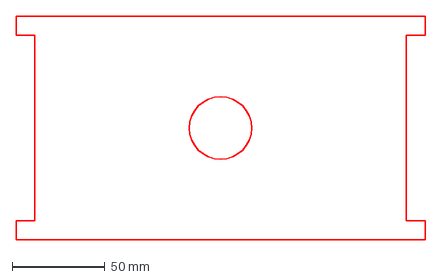
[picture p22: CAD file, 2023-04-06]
35/PlaqueTrouee.dxf
220.0 x 120.0 mm

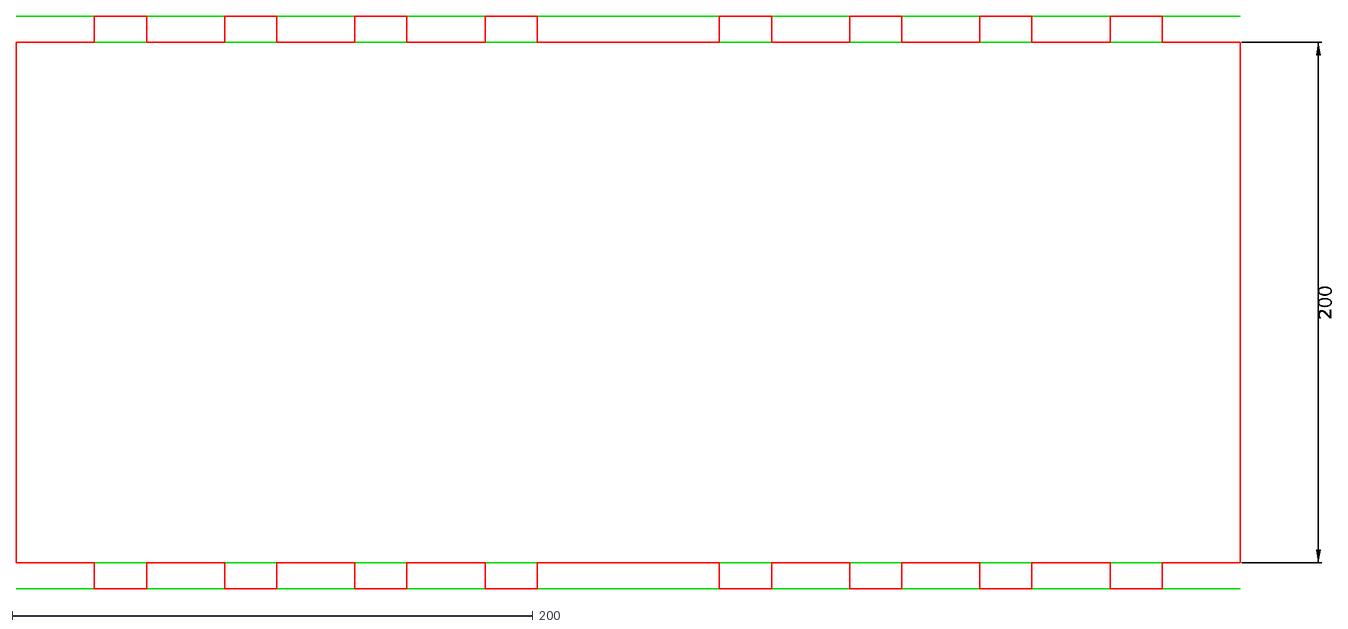
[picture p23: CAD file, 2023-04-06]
31/SupportFAA31TraverseVerticale.dxf
200

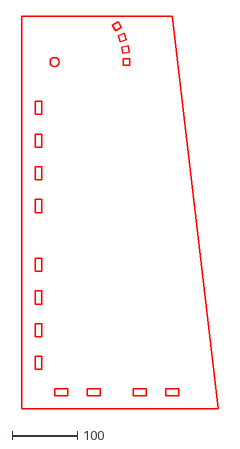
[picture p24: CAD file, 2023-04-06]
31/#SupportFAA31Droit.dxf
300.0 x 600.0

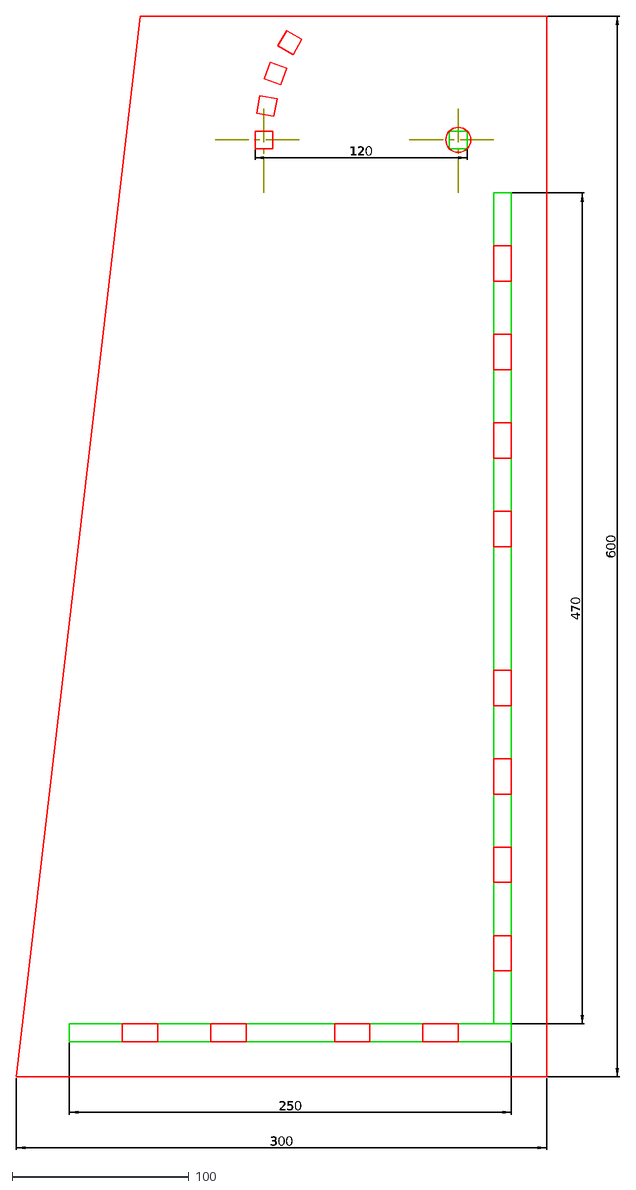
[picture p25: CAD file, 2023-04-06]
31/SupportFAA31Gauche.dxf
120
470
250
300
600

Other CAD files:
31/SupportFAAv3.1.dxf
31/SupportFAA31Droit.dxf

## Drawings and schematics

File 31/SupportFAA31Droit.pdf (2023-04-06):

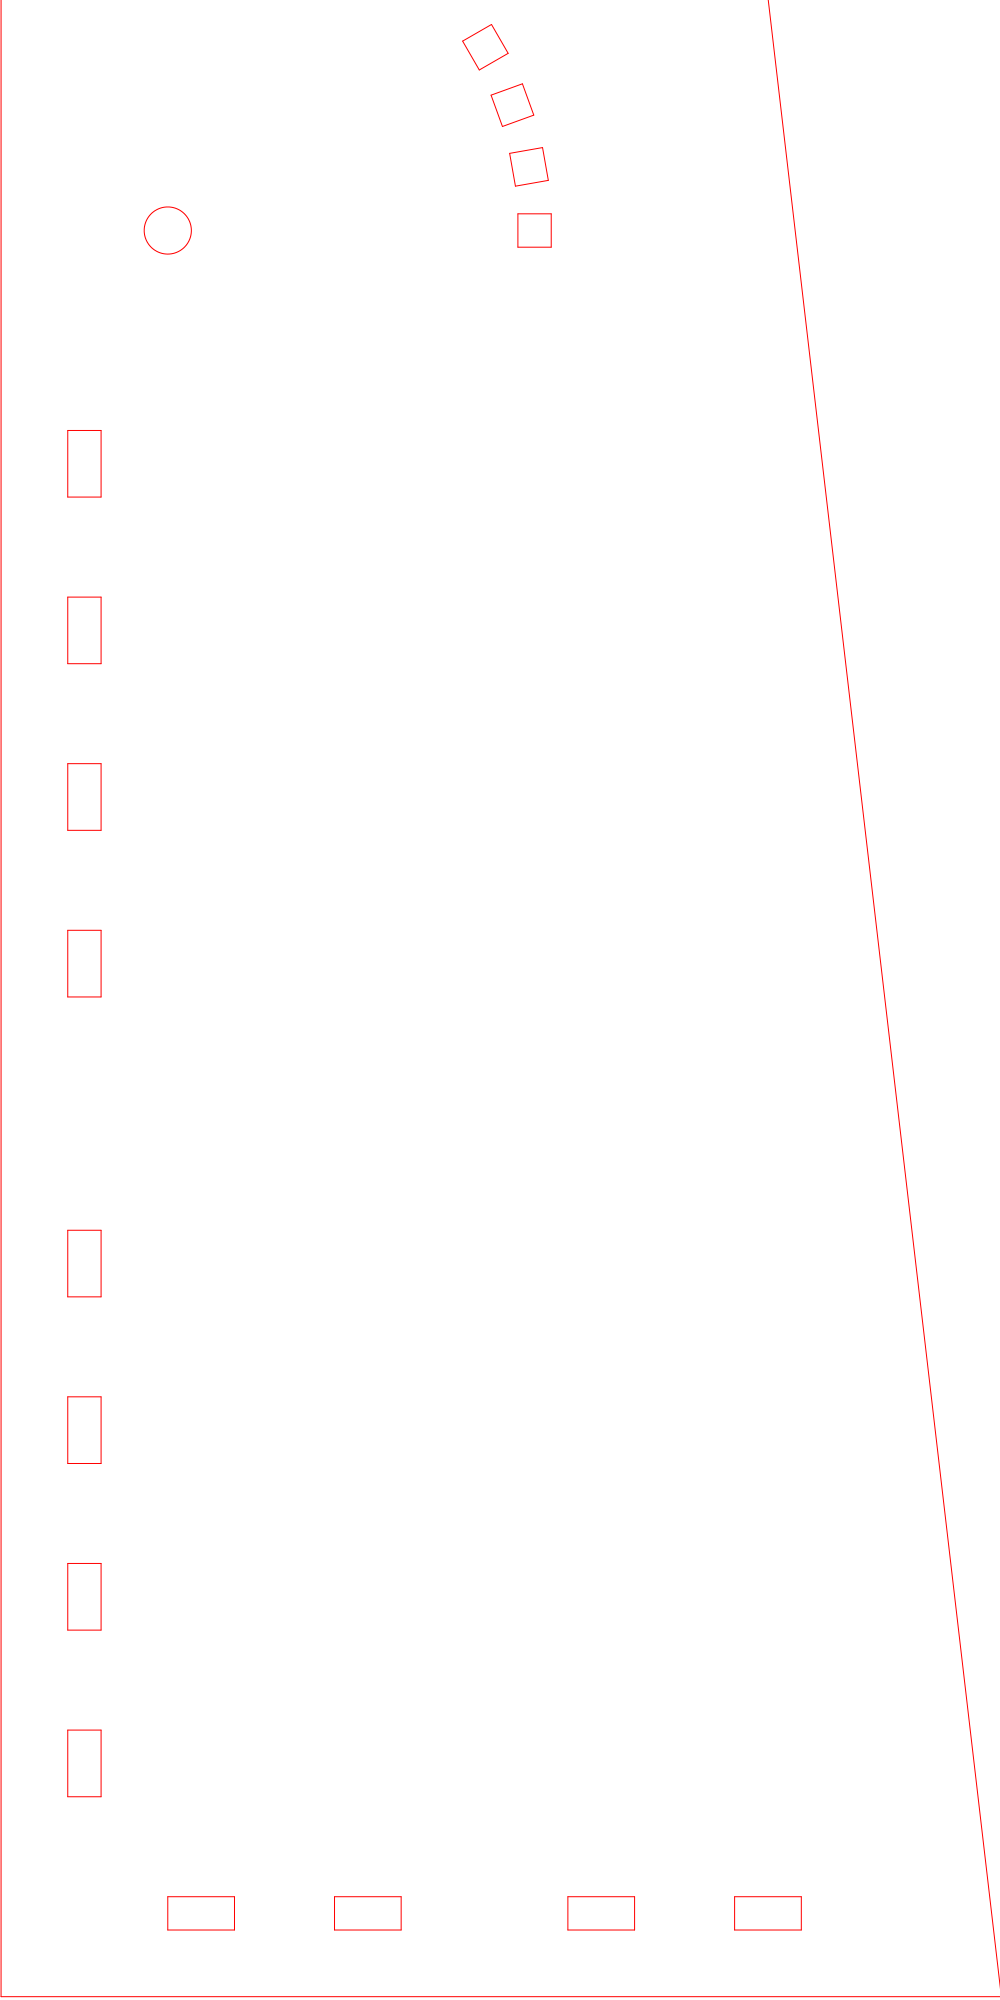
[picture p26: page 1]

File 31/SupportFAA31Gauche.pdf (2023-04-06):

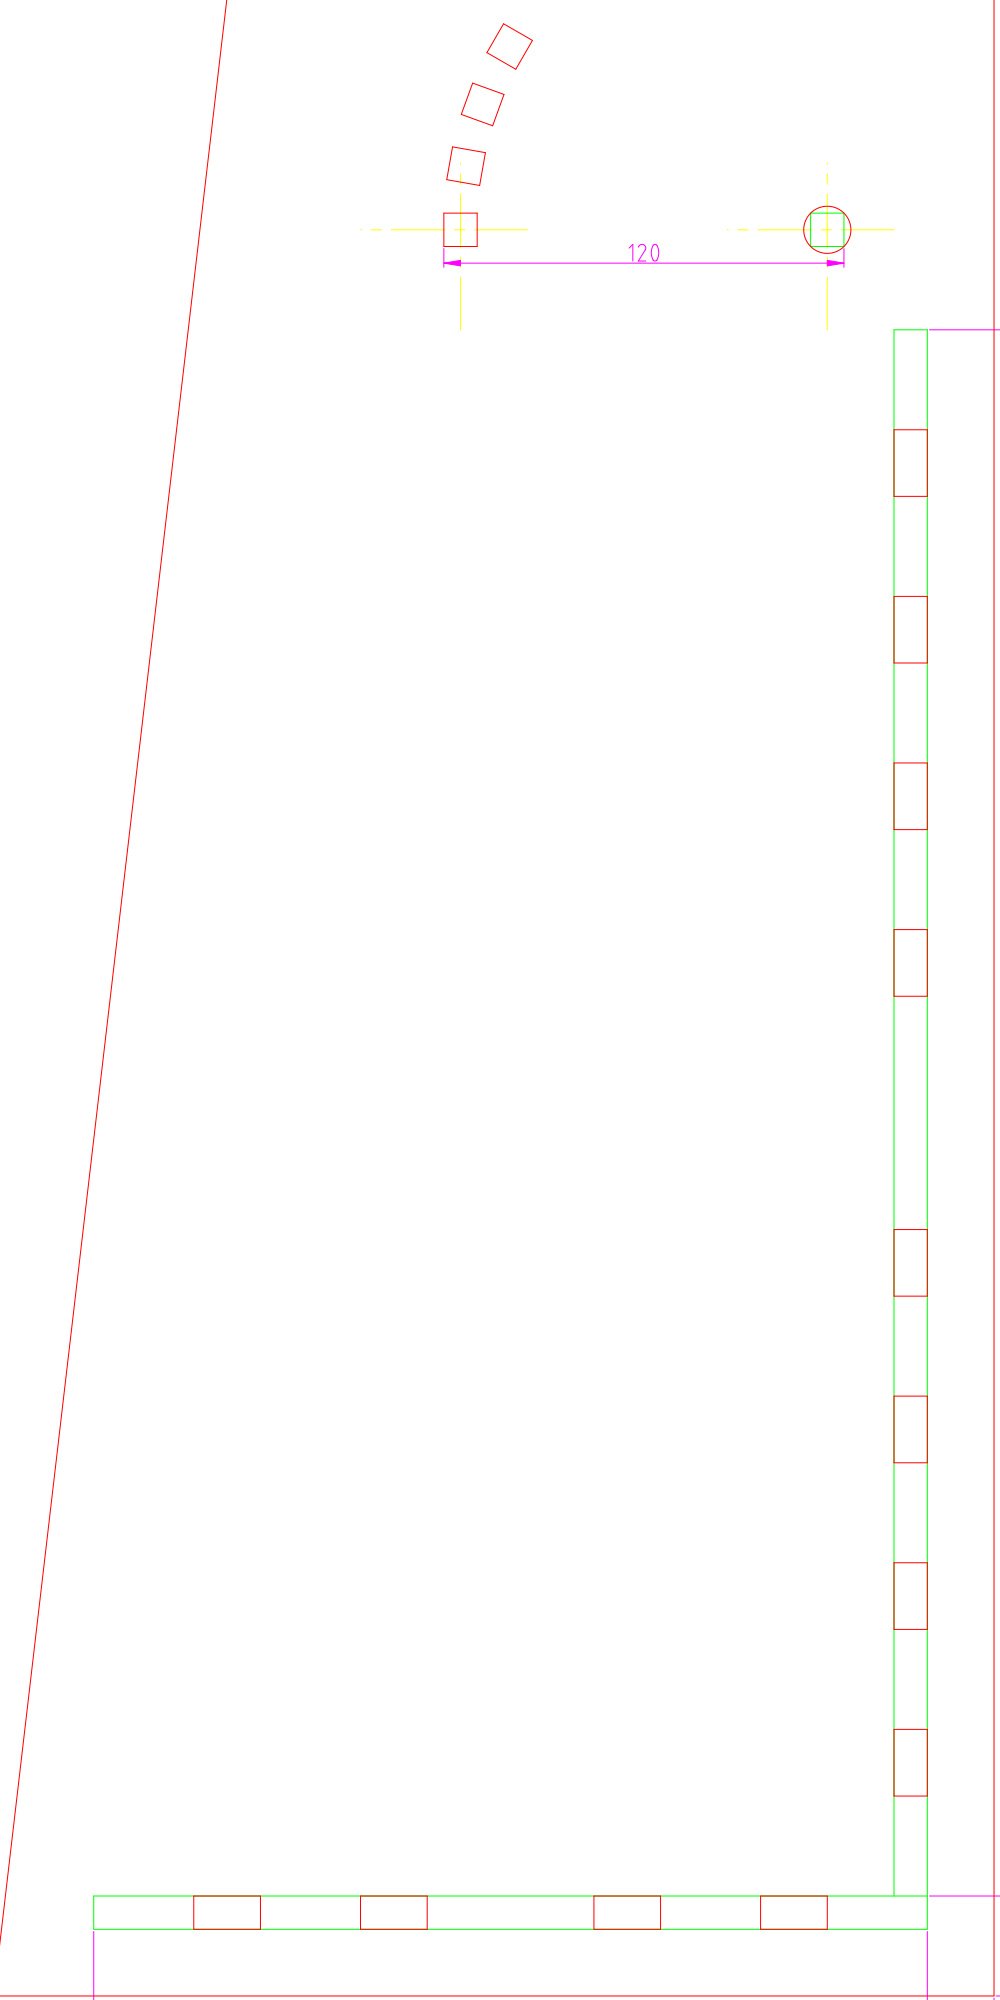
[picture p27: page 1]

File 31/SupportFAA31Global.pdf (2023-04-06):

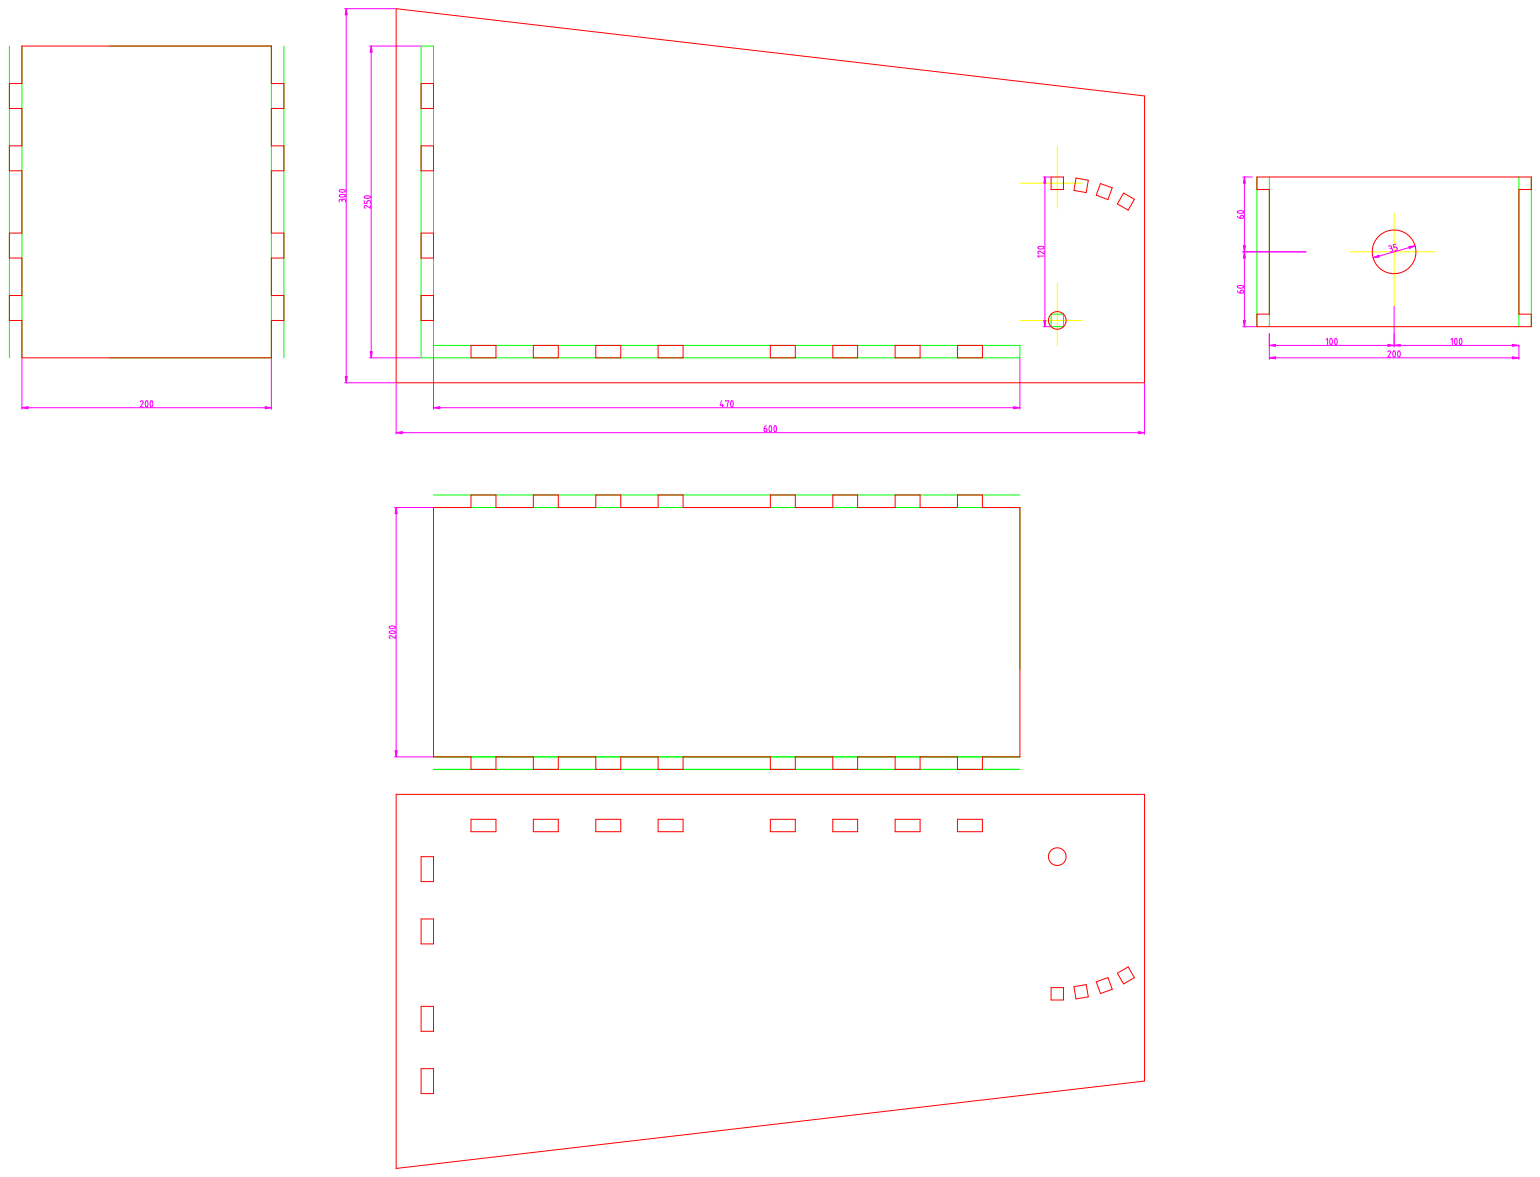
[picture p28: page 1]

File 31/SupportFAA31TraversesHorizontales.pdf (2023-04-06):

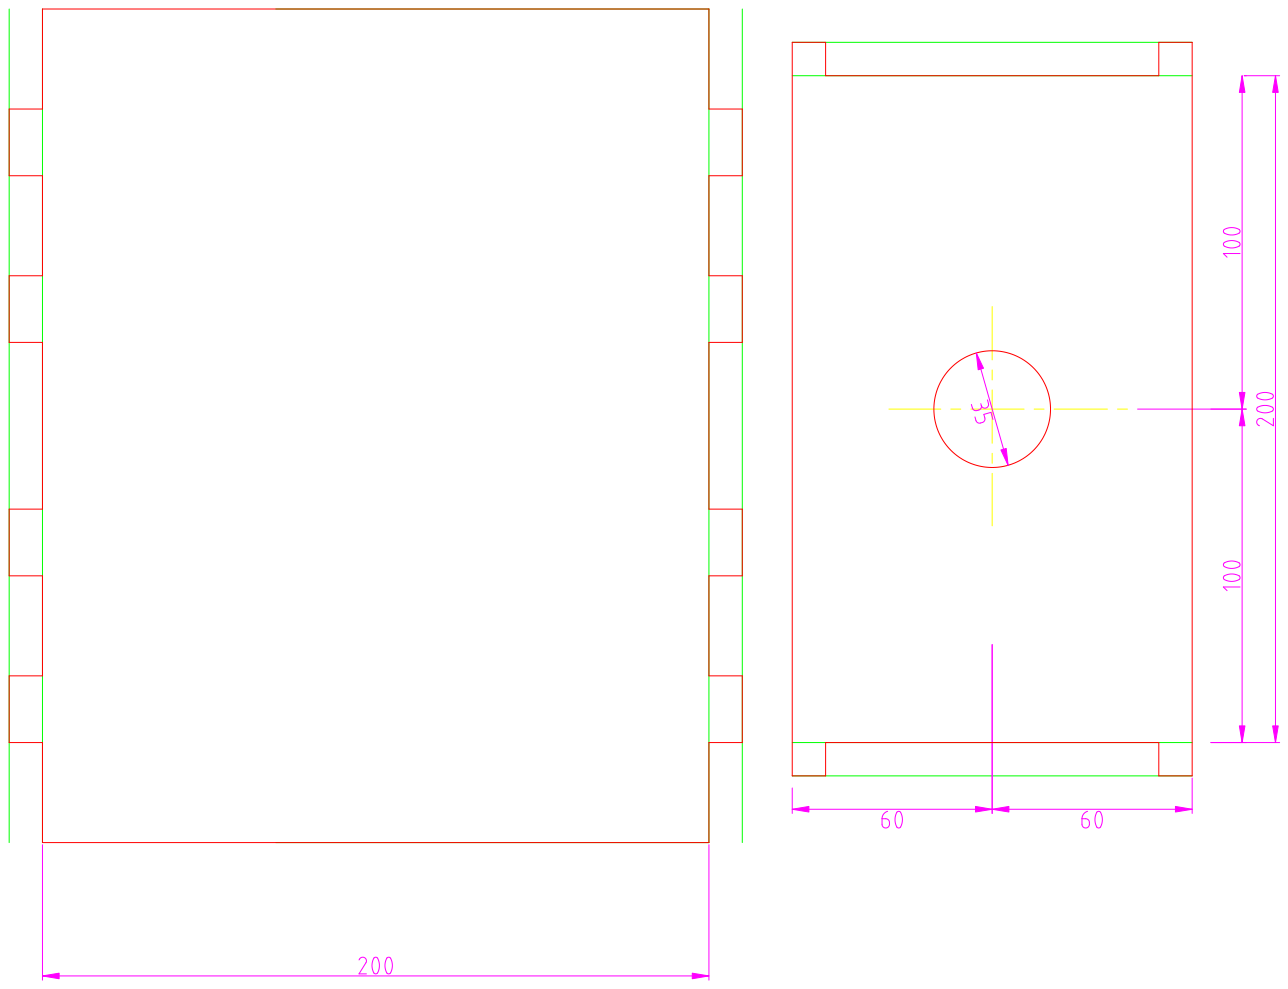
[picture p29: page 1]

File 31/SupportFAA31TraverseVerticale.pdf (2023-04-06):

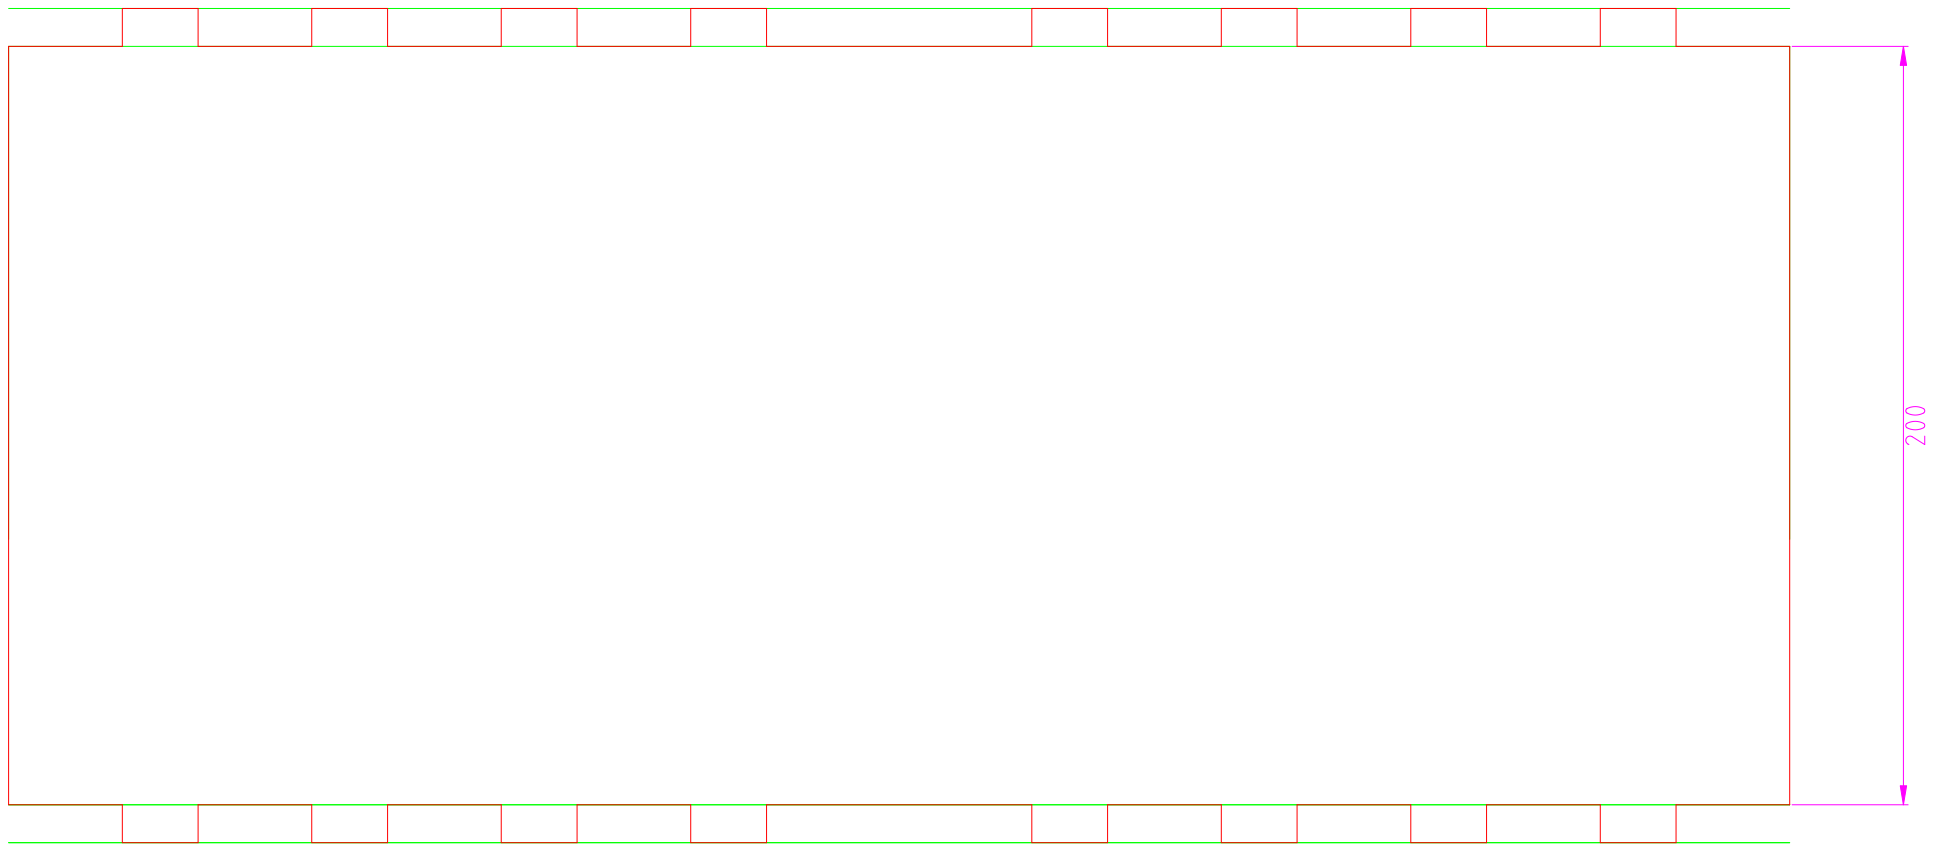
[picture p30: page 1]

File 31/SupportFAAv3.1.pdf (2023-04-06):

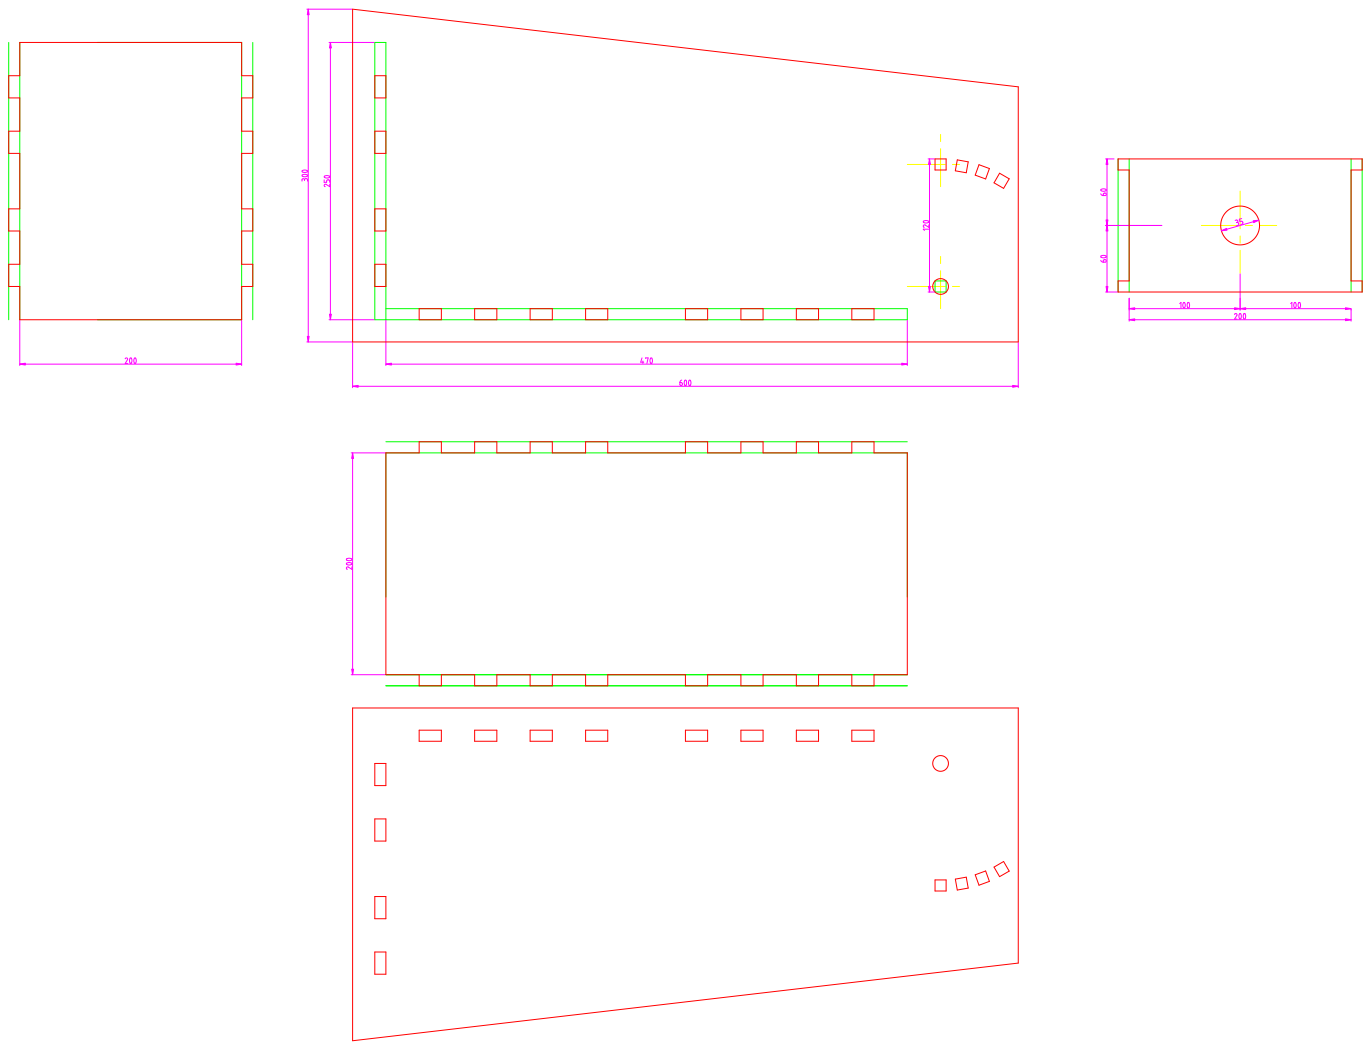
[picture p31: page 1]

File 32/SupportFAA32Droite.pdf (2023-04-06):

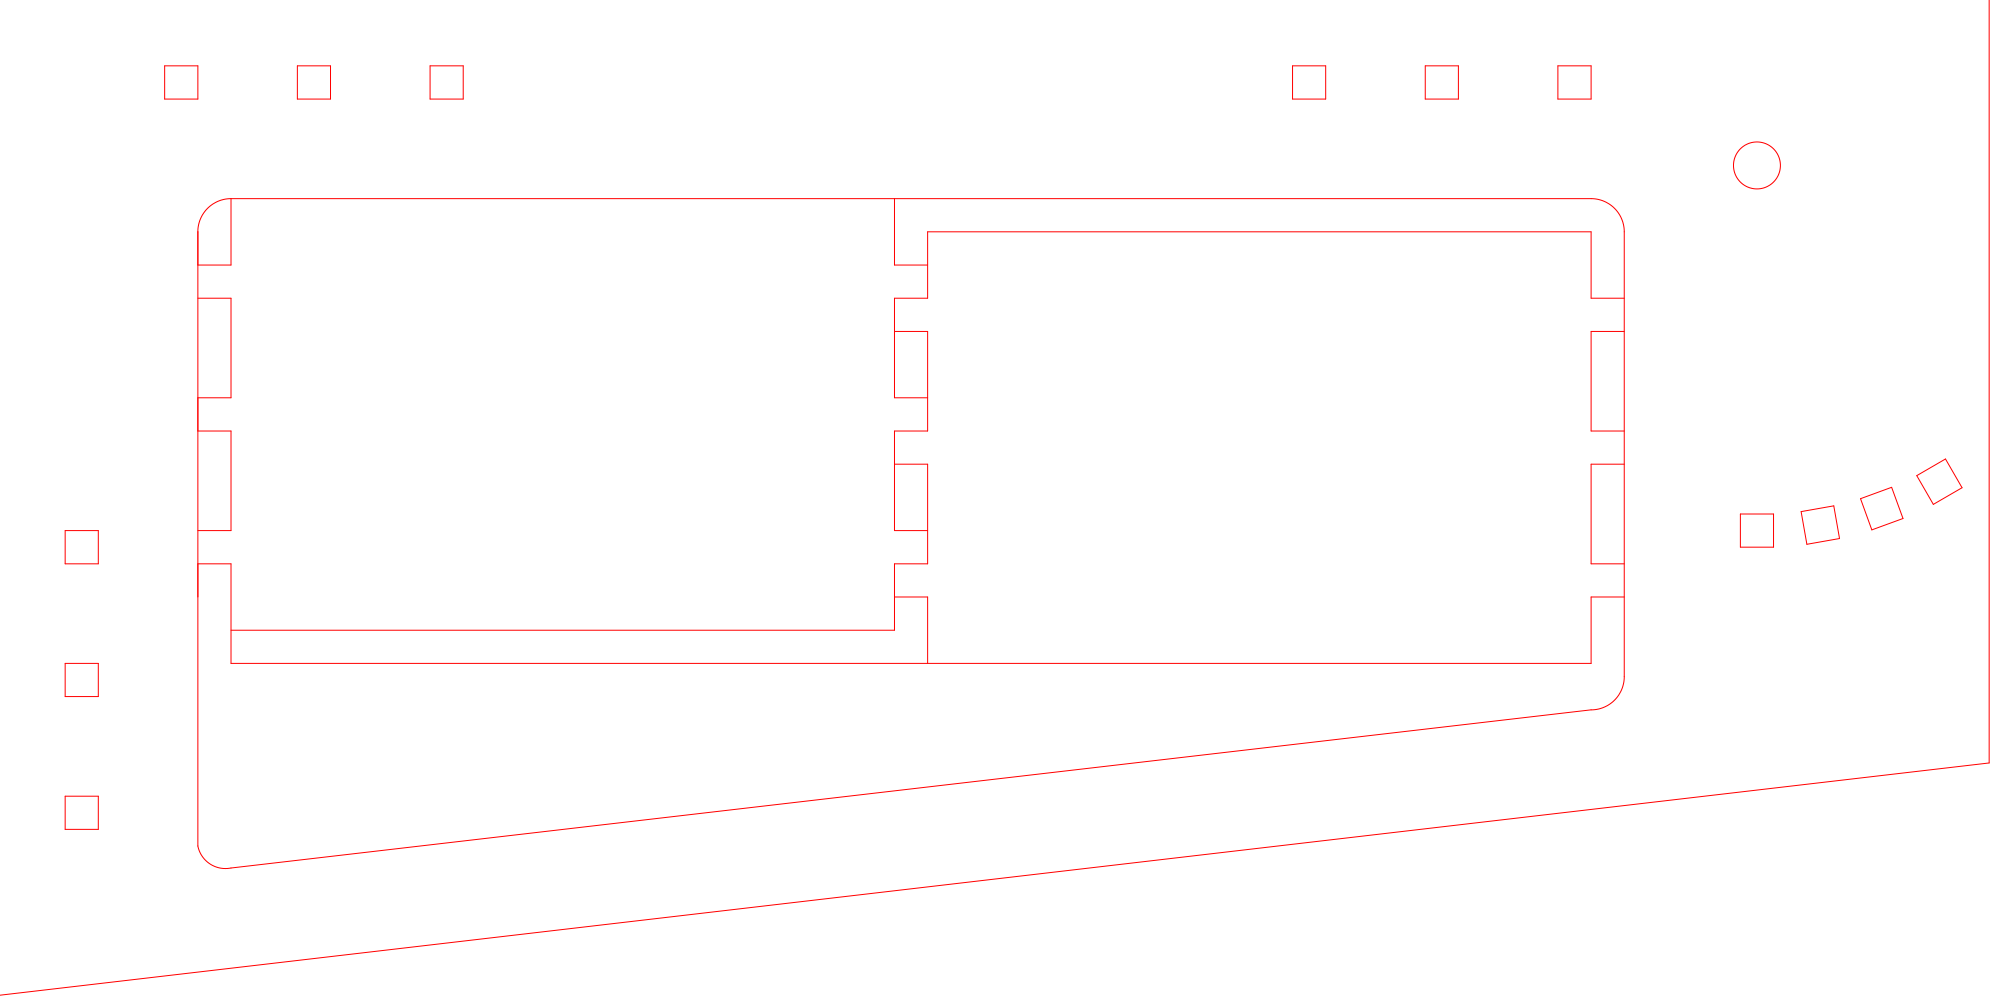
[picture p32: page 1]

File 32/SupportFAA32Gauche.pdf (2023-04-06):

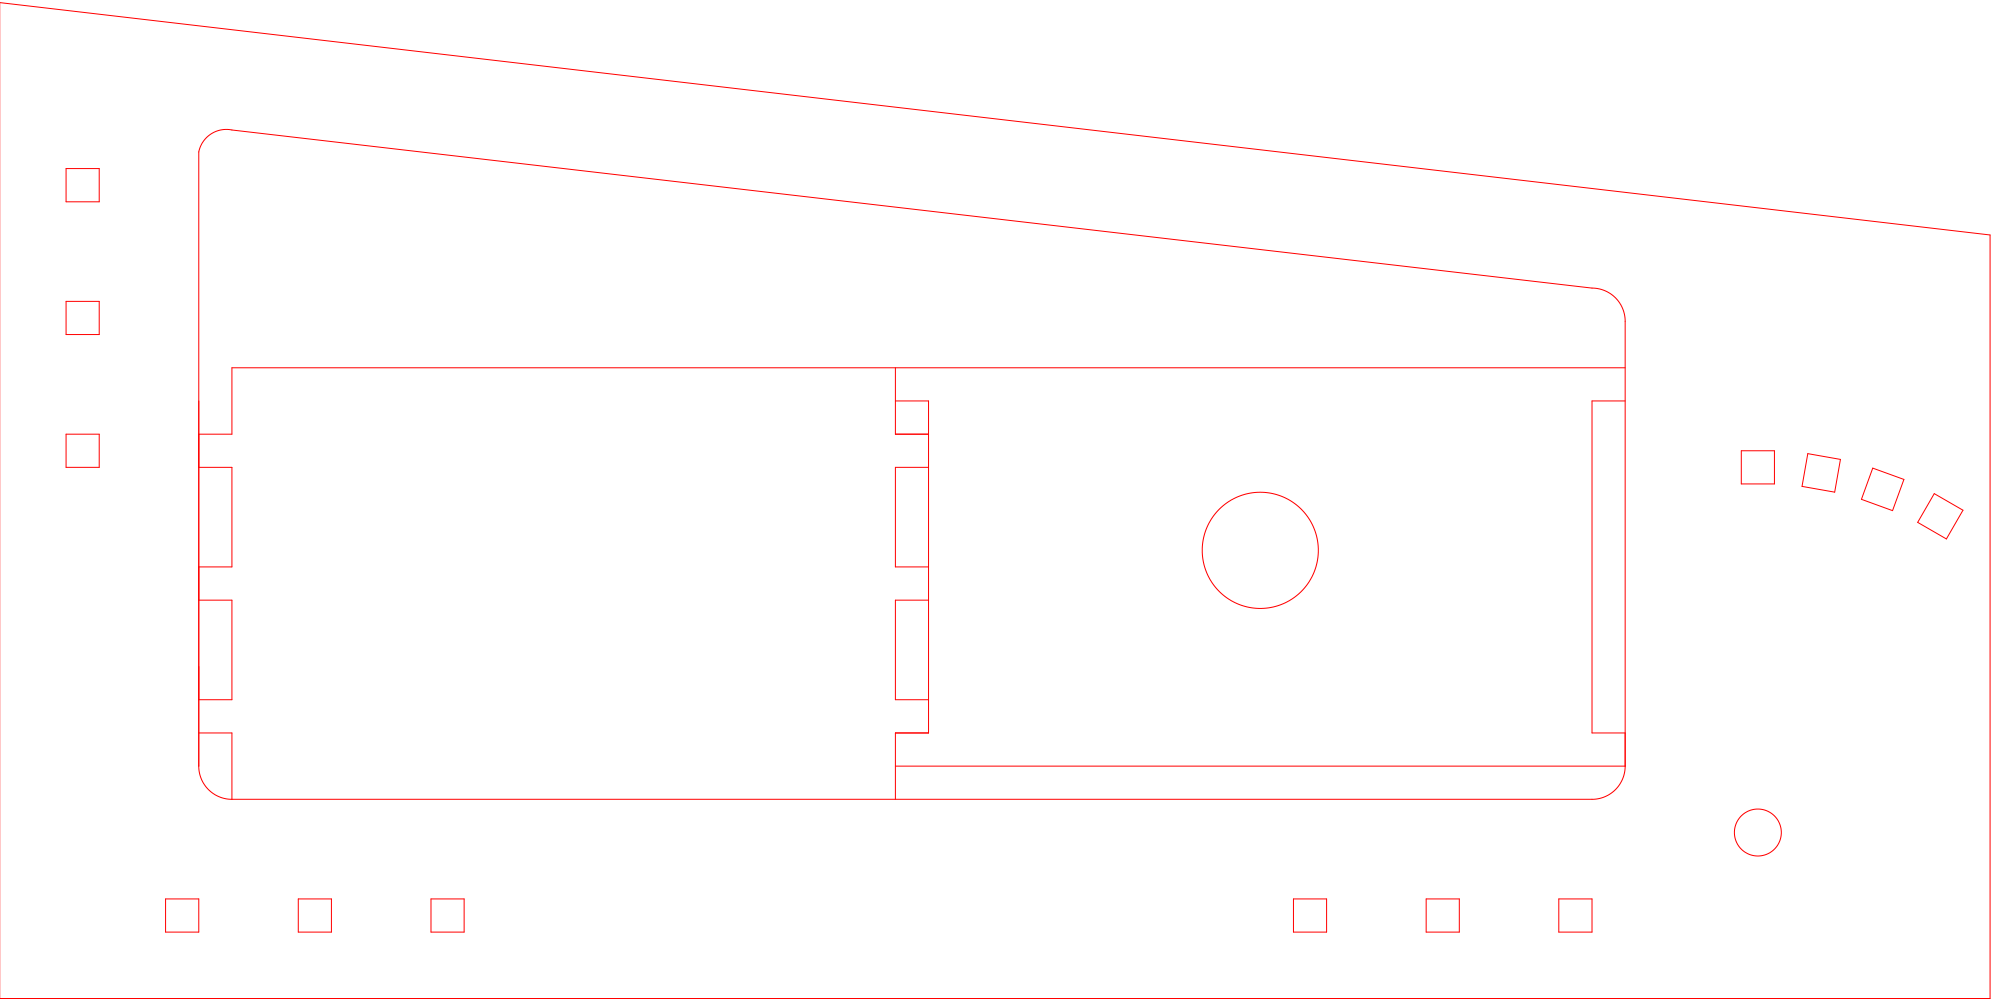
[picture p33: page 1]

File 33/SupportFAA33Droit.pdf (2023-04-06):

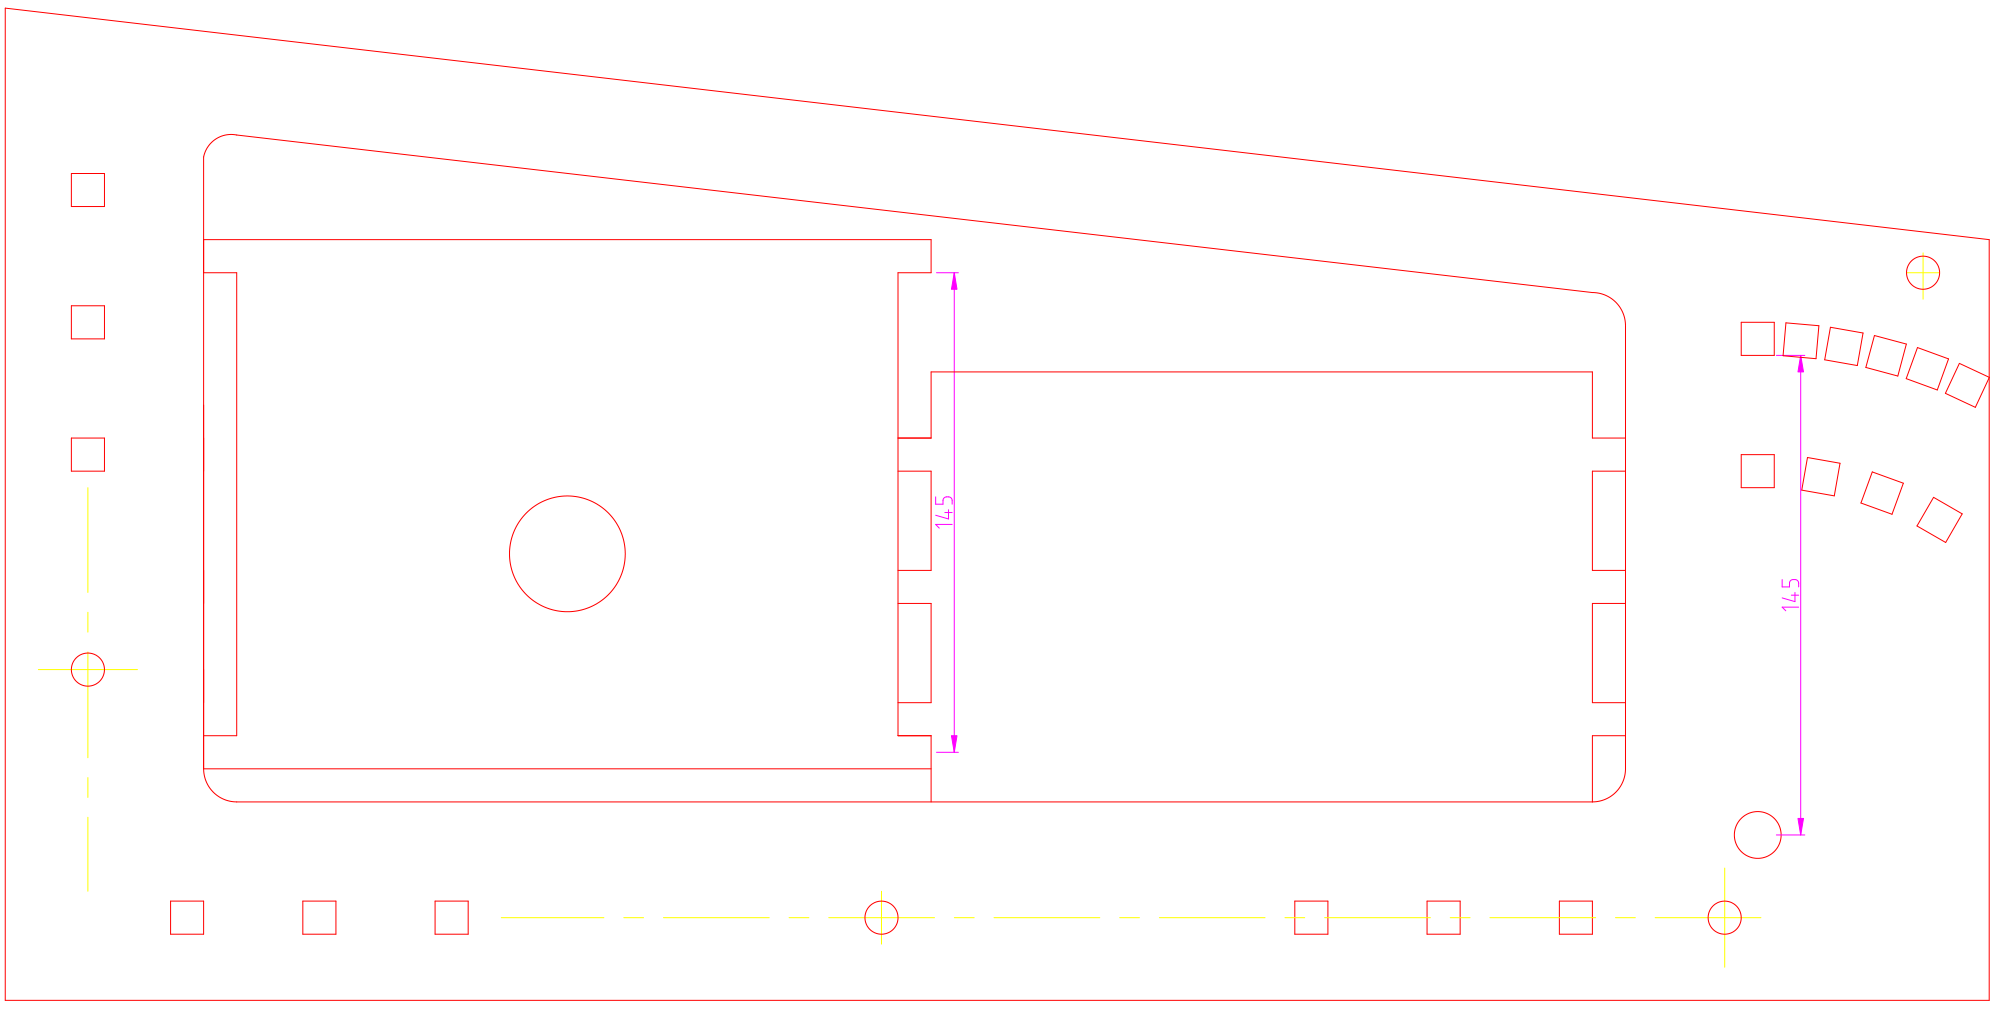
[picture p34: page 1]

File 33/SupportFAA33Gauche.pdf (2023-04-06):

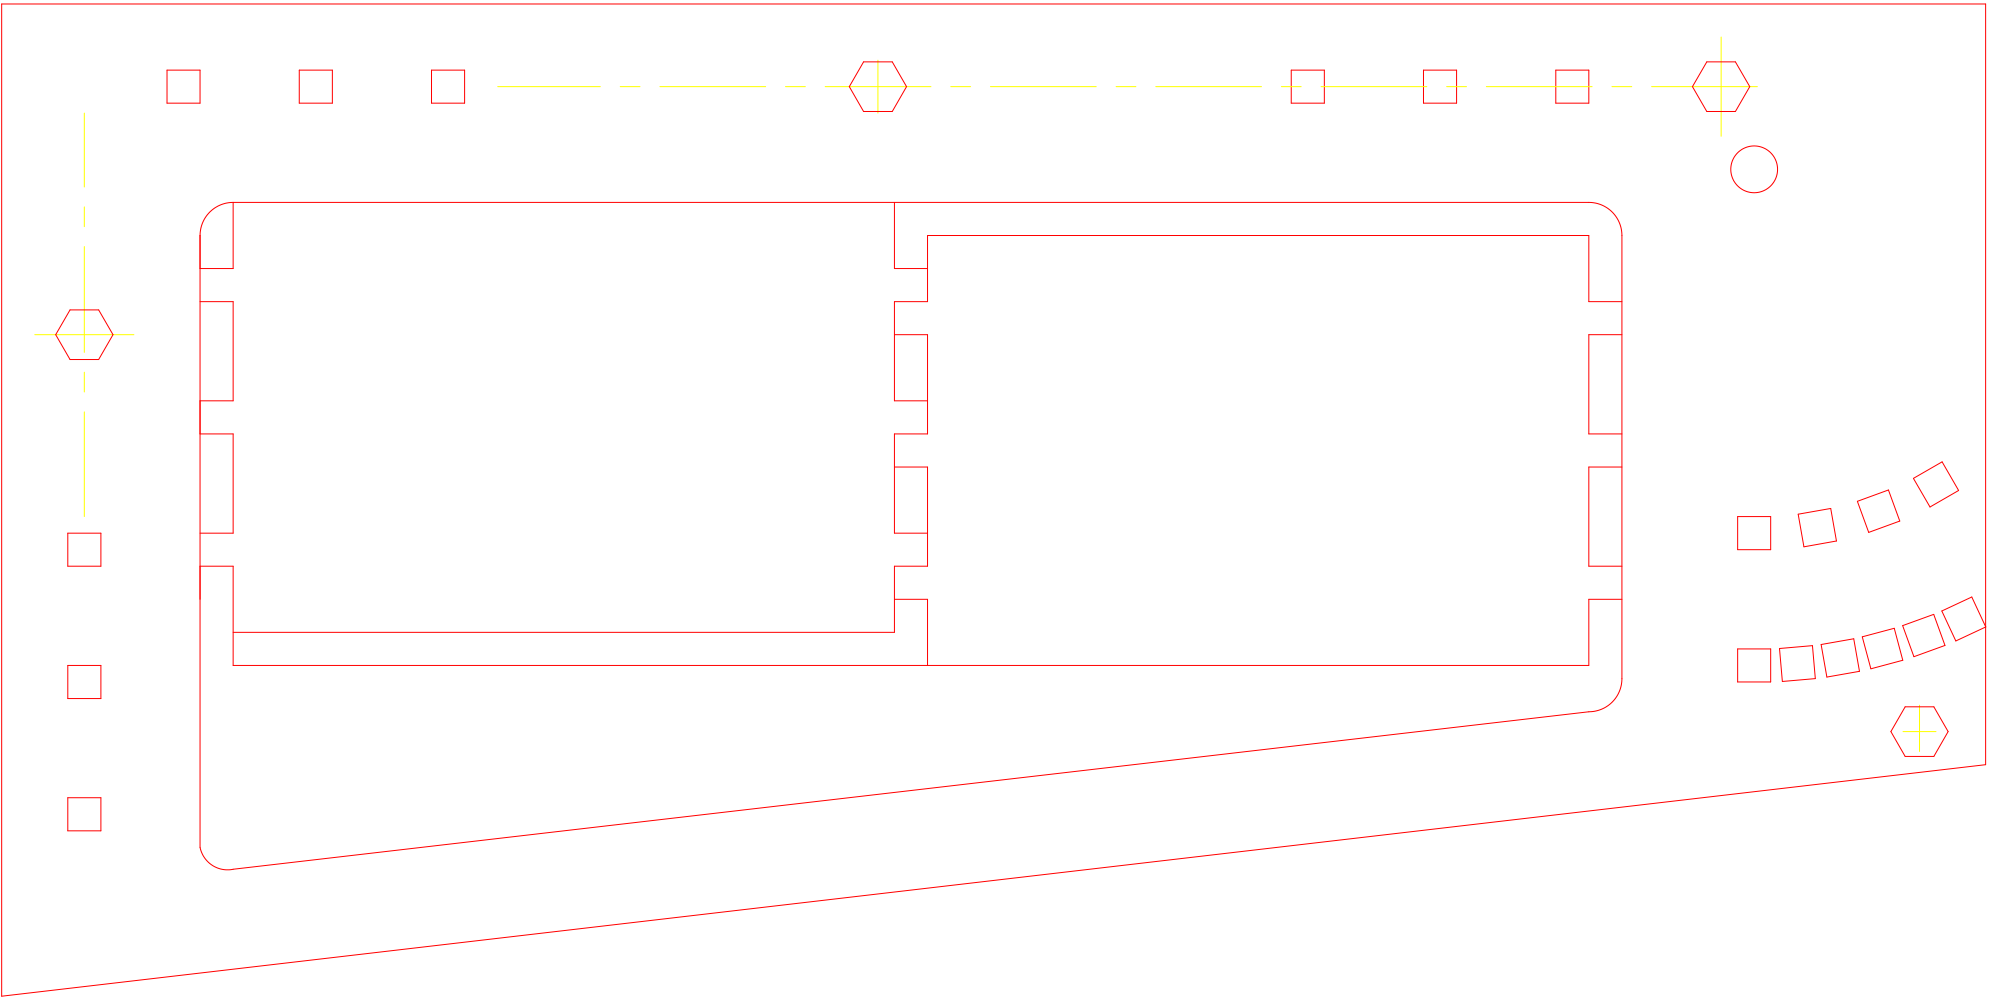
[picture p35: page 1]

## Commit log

2023-04-06 Chargement initial
    [#SupportFAA31Droit.dxf, BasesLancementFAA.ods, PlaqueTrouee.dxf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]
2023-04-06 Export traitement de texte
